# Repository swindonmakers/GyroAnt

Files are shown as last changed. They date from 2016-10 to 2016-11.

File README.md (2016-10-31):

# GyroAnt
Antweight tribute to [Gyrobot](http://www.gyrobot.co.uk/the-gyrobot.html) developed using OpenSCAD and the [OpenSCAD for Machine Design framework](https://github.com/swindonmakers/snhack.github.io/wiki/OpenSCADMD_Tutorial1).

See the [assembly, printing and sourcing guides](https://rawgit.com/swindonmakers/GyroAnt/master/hardware/docs/index.htm) for build instructions and links to the printable STLs.

https://rawgit.com/swindonmakers/GyroAnt/master/hardware/docs/index.htm

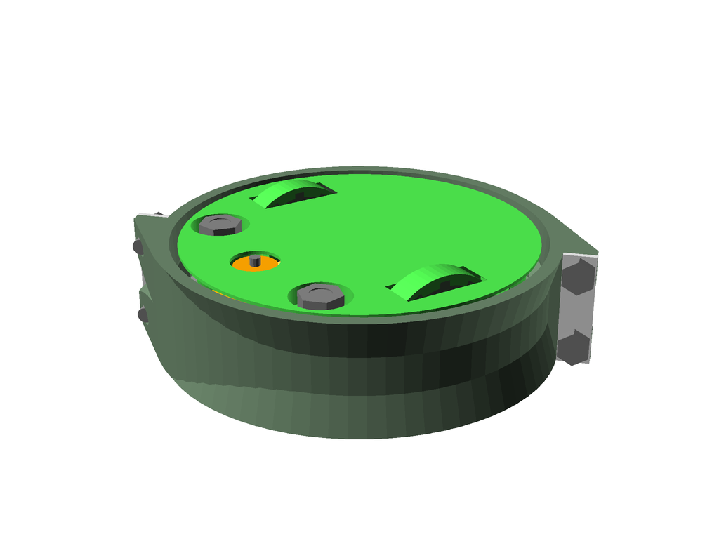
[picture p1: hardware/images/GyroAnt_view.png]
https://rawgit.com/swindonmakers/GyroAnt/master/hardware/docs/index.htm


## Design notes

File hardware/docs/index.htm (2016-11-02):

# GyroAnt Documentation

Design variants are listed below, with associated links to their assembly and printing guides. The Vitamin catalogue for the framework can be found at the bottom of the page.

## GyroAnt



### Guides

- GyroAnt Assembly Guide
- GyroAnt Printing Guide
- GyroAnt Sourcing Guide

## Vitamin Catalogue

Catalogue of the vitamins available within the Machine Design framework:

Vitamin Catalogue

NB: The catalogue may contain more vitamins than are actually used by the project

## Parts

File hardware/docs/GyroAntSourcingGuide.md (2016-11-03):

# GyroAnt
# Sourcing Guide

### 1x C2020 Micro Brushless Outrunner 3500kv 11g

Unit Cost | Source | Notes 
--- | --- | --- 
8.20 | [link](http://hobbyking.com) | 

 

### 1x DYS BLHeli 16A ESC

Unit Cost | Source | Notes 
--- | --- | --- 
3.20 | [link](http://hobbyking.com) | 

 

### 1x DasMikro Ultra Mini 8CH PPM Receiver

Unit Cost | Source | Notes 
--- | --- | --- 
9.14 | [link](http://www.banggood.com/FLYSKY-Ultra-Miniature-PPM-Signal-Output-8CH-Receiver-For-Multicopter-p-988175.html) | 

 

### 2x N20DCGearMotor

Unit Cost | Source | Notes 
--- | --- | --- 
2.64 | [link](http://cgi.ebay.co.uk/ws/eBayISAPI.dll?ViewItem&item=181946954392&var=481770476175) | 6V 200RPM version

 

### 2x O-Ring 2x10

Unit Cost | Source | Notes 
--- | --- | --- 
0 |  | No sources found

 

### 2x Stainless steel Flat Bar 6x1mm x 21mm

Unit Cost | Source | Notes 
--- | --- | --- 
0 |  | No sources found

 

### 2x Stainless steel Round Bar 2mm x 14mm

Unit Cost | Source | Notes 
--- | --- | --- 
0 |  | No sources found

 

### 2x TowerPro SG90 Driver

Unit Cost | Source | Notes 
--- | --- | --- 
2.00 | www.ebay.co.uk | 

 

### 1x Turnigy Nano-Tech 120mAh 2S 25C Lipo Pack E-Flite Compatible

Unit Cost | Source | Notes 
--- | --- | --- 
5.99 | [link](http://cgi.ebay.co.uk/ws/eBayISAPI.dll?ViewItem&item=331965220542) | 

 

### 3x 624VV 4x13x6mm V Groove Sealed Ball Bearing

Unit Cost | Source | Notes 
--- | --- | --- 
0.19 | [link](http://cgi.ebay.co.uk/ws/eBayISAPI.dll?ViewItem&item=221317556825&var=520193870489) | 

 

### 5x M4 Nut

Unit Cost | Source | Notes 
--- | --- | --- 
0.05 |  | No sources found

 

### 4x M3 hex screw x 8mm

Unit Cost | Source | Notes 
--- | --- | --- 
0.10 |  | No sources found

 

### 1x M4 hex screw x 15mm

Unit Cost | Source | Notes 
--- | --- | --- 
0.10 |  | No sources found

 

### 2x M4 hex screw x 19mm

Unit Cost | Source | Notes 
--- | --- | --- 
0.10 |  | No sources found

 

## Summary

### Total Costs

Metric | Value 
--- | --- 
Total Vitamins | 29
Total Cost (cheapest) | 37.33 GBP

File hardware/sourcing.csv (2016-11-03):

Vitamin | Cost | Source | Notes
C2020 Micro Brushless Outrunner 3500kv 11g | 8.20 | http://hobbyking.com
DYS BLHeli 16A ESC | 3.20 | http://hobbyking.com
DasMikro Ultra Mini 8CH PPM Receiver | 9.14 | http://www.banggood.com/FLYSKY-Ultra-Miniature-PPM-Signal-Output-8CH-Receiver-For-Multicopter-p-988175.html
N20DCGearMotor | 2.64 | http://cgi.ebay.co.uk/ws/eBayISAPI.dll?ViewItem&item=181946954392&var=481770476175 | 6V 200RPM version
O-Ring 2x10 | 0 |  | No sources found
Stainless steel Flat Bar 6x1mm x 21mm | 0 |  | No sources found
Stainless steel Round Bar 2mm x 14mm | 0 |  | No sources found
TowerPro SG90 Driver | 2.00 | www.ebay.co.uk
Turnigy Nano-Tech 120mAh 2S 25C Lipo Pack E-Flite Compatible | 5.99 | http://cgi.ebay.co.uk/ws/eBayISAPI.dll?ViewItem&item=331965220542
624VV 4x13x6mm V Groove Sealed Ball Bearing | 0.19 | http://cgi.ebay.co.uk/ws/eBayISAPI.dll?ViewItem&item=221317556825&var=520193870489
M4 Nut | 0.05 |  | No sources found
M3 hex screw x 8mm | 0.10 |  | No sources found
M4 hex screw x 15mm | 0.10 |  | No sources found
M4 hex screw x 19mm | 0.10 |  | No sources found

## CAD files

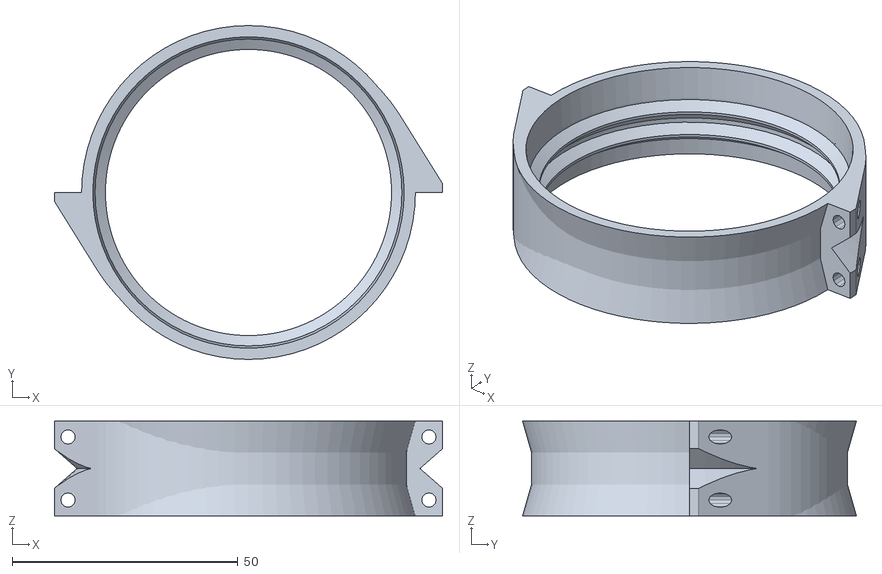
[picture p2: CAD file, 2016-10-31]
hardware/printedparts/stl/WeaponRing.stl
86.0 x 74.0 x 21.0

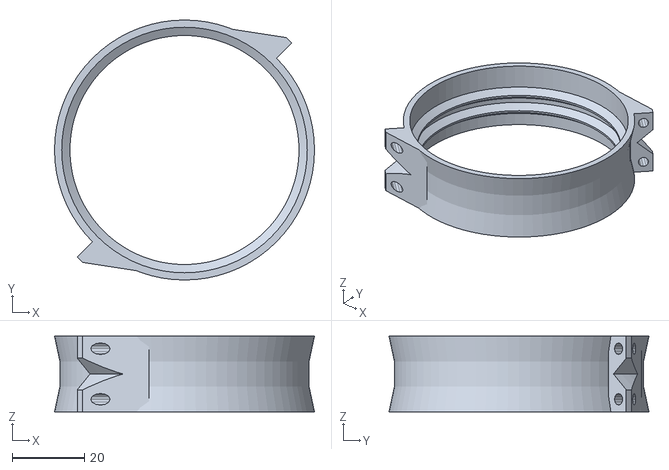
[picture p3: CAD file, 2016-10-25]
hardware/sandbox/WeaponRing.stl
72.0 x 72.0 x 21.0

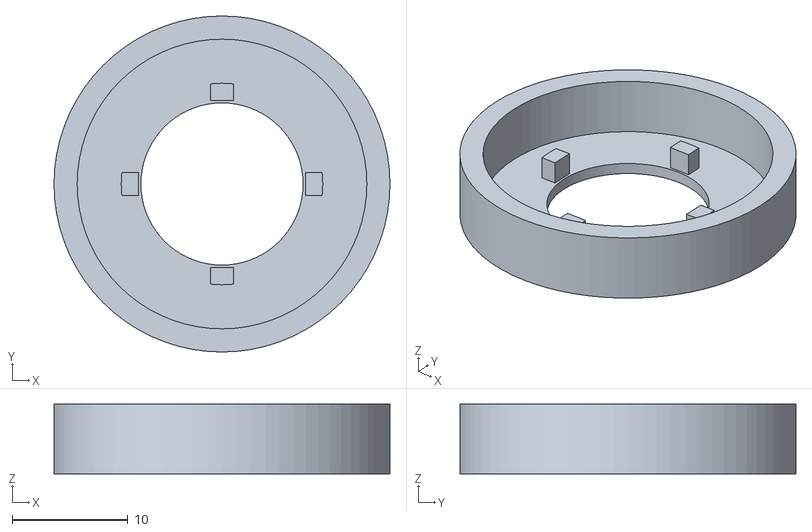
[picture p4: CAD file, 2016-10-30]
hardware/printedparts/stl/TyreMould.stl
29.0 x 29.0 x 6.00

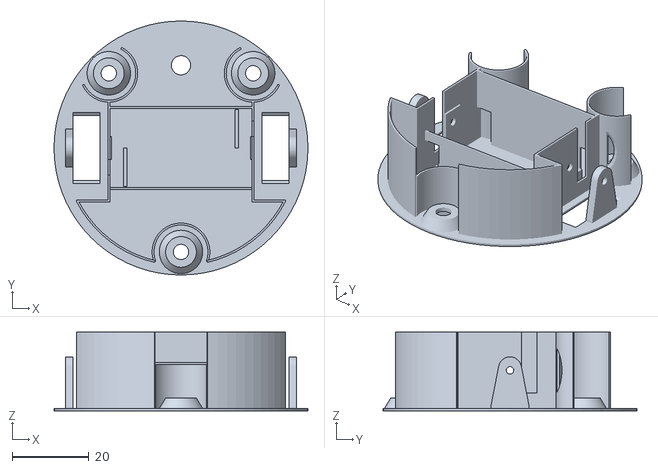
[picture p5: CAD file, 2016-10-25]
hardware/sandbox/Base.stl
66.0 x 66.0 x 20.4

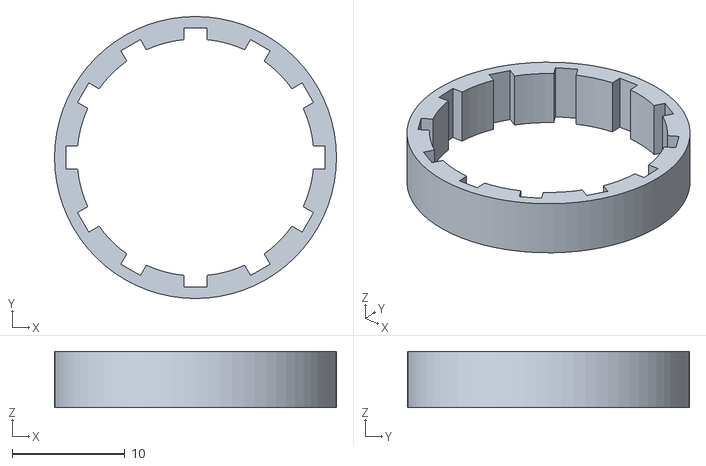
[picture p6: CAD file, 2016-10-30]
hardware/printedparts/stl/Tyre.stl
25.0 x 25.0 x 5.00

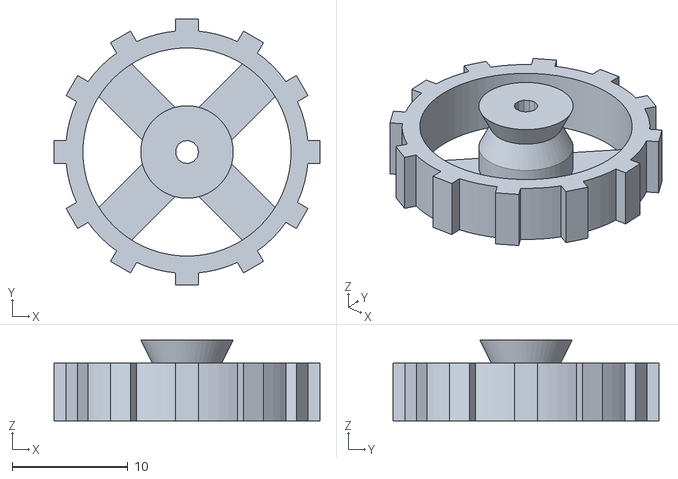
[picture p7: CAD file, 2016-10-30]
hardware/printedparts/stl/Wheel.stl
23.0 x 23.0 x 7.00

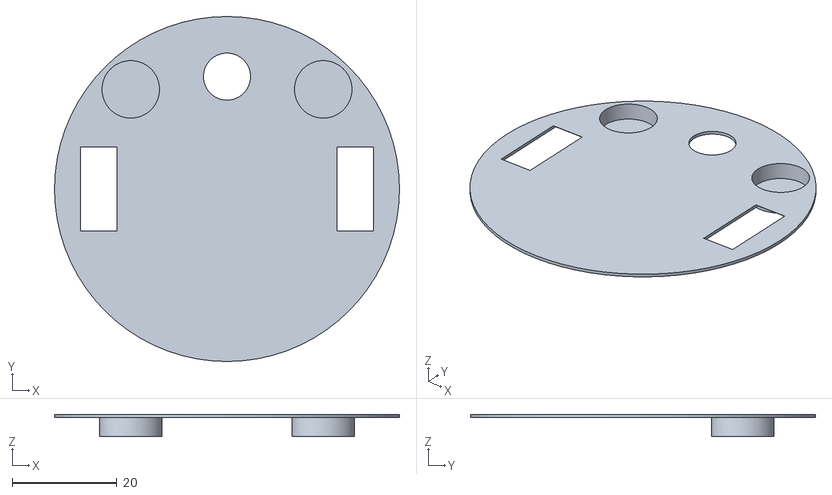
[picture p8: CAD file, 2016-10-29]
hardware/printedparts/stl/Lid.stl
66.0 x 66.0 x 4.30

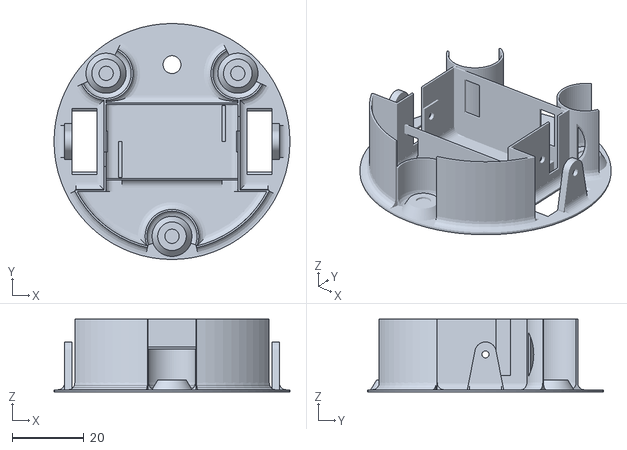
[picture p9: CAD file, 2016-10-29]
hardware/printedparts/stl/Base.stl
66.0 x 66.0 x 20.4

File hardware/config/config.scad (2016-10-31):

//
// Config
//

// Coding-style
// ------------
//
// Global variables are written in UpperCamelCase.
// A logical hierarchy should be indicated using underscores, for example:
//     StepperMotor_Connections_Axle
//
// Global short-hand references should be kept to a minimum to avoid name-collisions

// Framework configuration
include <../framework/config/config.scad>


// Put overrides to framework config here
ColourScheme = 1;


// Machine specific global parameters here
// common wall thicknesses for printed parts
DefaultWall 	= 4*perim;
ThickWall 		= 8*perim;
// short-hand
dw 				= DefaultWall;
tw 				= ThickWall;

// Global design parameters
WheelOD = 25;
TyreThickness = 2;
WeaponOR = 74/2;
RingThickness = 3;
GroundClearance = 2;
BearingAngles = [46, 134, 270];
BearingOffset = WeaponOR-RingThickness-7-0.5;
BearingHeight = 8; // from ground plane
ToothScrewSpacing = 14;



// Include all other project specific configuration files
include <utils.scad>
include <vitamins.scad>
include <cutparts.scad>
include <printedparts.scad>
include <assemblies.scad>

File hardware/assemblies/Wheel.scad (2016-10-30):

module WheelAssembly () {

    assembly("assemblies/Wheel.scad", "Wheel", str("WheelAssembly()")) {

        // generate an animation video for this assembly
        animation(title="Wheel",framesPerStep=10);

        // base part
        Wheel_STL();

        // steps
        CurStep = $ShowStep;
        step(1, "Place wheel hub into the tyre mould") {
            view(t=[0,0,0], r=[52,0,218], d=240);


            if (CurStep<3 || $ShowBOM)
                attach([[0,0,-1], [0,0,1], 0,0,0], DefConUp)
                  TyreMould_STL();
        }

        AnimT = $AnimateExplodeT;
        step(2, "Pour in rubber to overmould the tyre") {
            view(t=[0,0,0], r=[52,0,218], d=240);

            translate([0,0,0])
                scale([1,1,CurStep==2 ? AnimT : 1])
                  Tyre_STL();


        }


        step(3, "Once dry, remove the finished tyre from the mould") {
            view(t=[0,0,0], r=[52,0,218], d=240);

            if (CurStep<4 || $ShowBOM)
                attach([[0,0,-11], [0,0,-1], 0,0,0], DefConDown)
                TyreMould_STL();
        }



    }
}

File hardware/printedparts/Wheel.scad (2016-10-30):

// Connectors

Wheel_Con_Def = [[0,0,0], [0,0,-1], 0,0,0];


module Wheel_STL() {

    printedPart("printedparts/Wheel.scad", "Wheel", "Wheel_STL()") {

        view(t=[0,0,0],r=[72,0,130],d=400);

        if (DebugCoordinateFrames) frame();
        if (DebugConnectors) {
            connector(Wheel_Con_Def);
        }

        color(Level4PlasticColor) {
            if (UseSTL) {
                import(str(STLPath, "Wheel.stl"));
            } else {
                Wheel_Model();
            }
        }
    }
}


module Wheel_Model()
{
    t =1.5;
    h= 5;
    difference() {
        union() {
            // tyre
            tube(WheelOD/2 - TyreThickness, WheelOD/2-TyreThickness-t, h=h, center=false);

            // spokes
            for (i=[0:3])
                rotate([0,0,i*360/4 + 45])
                translate([0,-2,0])
                cube([WheelOD/2-TyreThickness-1, 4, 1]);

            // keys for tyre
            nk = 12;
            for (i=[0:nk-1])
                rotate([0,0,i*360/nk])
                translate([WheelOD/2-TyreThickness-1,-1,0])
                cube([TyreThickness, 2, h]);

            // hub
            cylinder(r=8/2, h=3);

            // vslot
            translate([0,0,5])
                for(i=[0,1])
                mirror([0,0,i])
                cylinder(r1=3, r2=4, h=2);
        }

        // shaft
        cylinder(r=2/2, h=100, center=true);
    }
}

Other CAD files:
hardware/GyroAnt.scad
hardware/assemblies/Final.scad
hardware/assemblies/WeaponRing.scad
hardware/config/assemblies.scad
hardware/config/cutparts.scad
hardware/config/printedparts.scad
hardware/config/utils.scad
hardware/config/vitamins.scad
hardware/cutparts/HammerPlate.scad
hardware/printedparts/Base.scad
hardware/printedparts/Lid.scad
hardware/printedparts/Tyre.scad
hardware/printedparts/TyreMould.scad
hardware/printedparts/WeaponRing.scad
hardware/sandbox/animatedAssembly.scad
hardware/sandbox/assembly_FinalAssembly.scad
hardware/sandbox/assembly_WeaponRingAssembly.scad
hardware/sandbox/assembly_WheelAssembly.scad
hardware/sandbox/cutpart_Axle.scad
hardware/sandbox/cutpart_HammerPlate.scad
hardware/sandbox/layout.scad
hardware/sandbox/printedpart_Base.scad
hardware/sandbox/printedpart_Lid.scad
hardware/sandbox/printedpart_Tyre.scad
hardware/sandbox/printedpart_TyreMould.scad
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

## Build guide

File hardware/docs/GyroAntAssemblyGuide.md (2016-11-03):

# GyroAnt
# Assembly Guide

view

## Bill of Materials

Make sure you have all of the following parts before you begin.

### Vitamins

Qty | Vitamin | Image
--- | --- | ---
1 | [C2020 Micro Brushless Outrunner 3500kv 11g]() |  | 
1 | [DYS BLHeli 16A ESC]() |  | 
1 | [DasMikro Ultra Mini 8CH PPM Receiver]() |  | 
2 | [N20DCGearMotor]() |  | 
2 | [O-Ring 2x10]() |  | 
2 | [Stainless steel Flat Bar 6x1mm x 21mm]() |  | 
2 | [Stainless steel Round Bar 2mm x 14mm]() |  | 
2 | [TowerPro SG90 Driver]() |  | 
1 | [Turnigy Nano-Tech 120mAh 2S 25C Lipo Pack E-Flite Compatible]() |  | 
3 | [624VV 4x13x6mm V Groove Sealed Ball Bearing]() |  | 
5 | [M4 Nut]() |  | 
4 | [M3 hex screw x 8mm]() |  | 
1 | [M4 hex screw x 15mm]() |  | 
2 | [M4 hex screw x 19mm]() |  | 

### Cut Parts

Qty | Part Name | Image
--- | --- | ---
2 | HammerPlate |  | 

### Printed Parts

Qty | Part Name | Image
--- | --- | ---
1 | [Base](../printedparts/stl/Base.stl) |  | 
1 | [Lid](../printedparts/stl/Lid.stl) |  | 
4 | [Tyre Mould](../printedparts/stl/TyreMould.stl) |  | 
2 | [Tyre](../printedparts/stl/Tyre.stl) |  | 
1 | [WeaponRing](../printedparts/stl/WeaponRing.stl) |  | 
2 | [Wheel](../printedparts/stl/Wheel.stl) |  | 

**Plastic Required**

32.6cm3, 0.04KG,  approx: 0.53 GBP

# Cutting Instructions

## HammerPlate (x2)

### Vitamins

Qty | Vitamin | Image
--- | --- | ---
2 | [Stainless steel Flat Bar 6x1mm x 21mm]() |  | 

### Fabrication Steps

1. Cut a small piece of 1mm steel plate to size

2. Drill two 3mm dia holes at 14mm spacing


# Assembly Instructions

## Wheel (x2)

### Printed Parts

Qty | Part Name | Image
--- | --- | ---
4 | [Tyre Mould](../printedparts/stl/TyreMould.stl) |  | 
2 | [Tyre](../printedparts/stl/Tyre.stl) |  | 
2 | [Wheel](../printedparts/stl/Wheel.stl) |  | 

### Assembly Animation

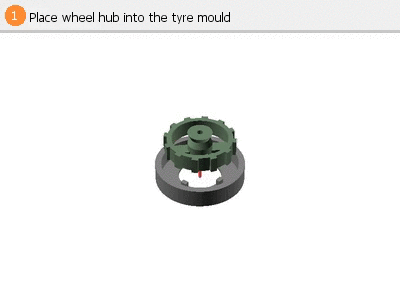
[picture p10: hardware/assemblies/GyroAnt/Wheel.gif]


### Assembly Steps

1. Place wheel hub into the tyre mould
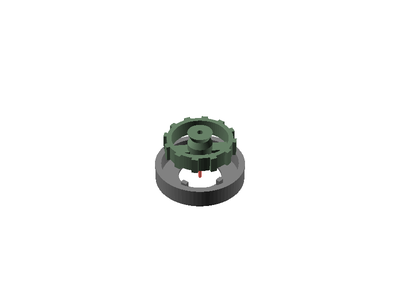
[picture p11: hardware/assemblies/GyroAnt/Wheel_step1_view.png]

2. Pour in rubber to overmould the tyre
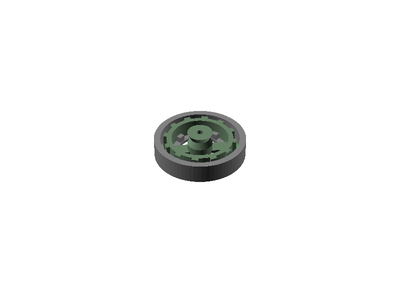
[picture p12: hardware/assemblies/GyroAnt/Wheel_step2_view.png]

3. Once dry, remove the finished tyre from the mould
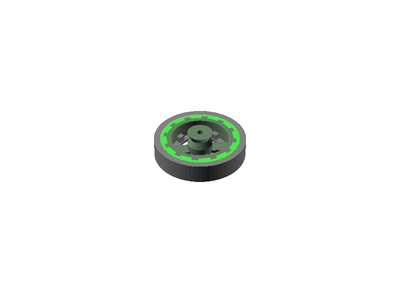
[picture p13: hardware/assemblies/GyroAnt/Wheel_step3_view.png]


## WeaponRing

### Vitamins

Qty | Vitamin | Image
--- | --- | ---
4 | [M3 hex screw x 8mm]() |  | 

### Printed Parts

Qty | Part Name | Image
--- | --- | ---
1 | [WeaponRing](../printedparts/stl/WeaponRing.stl) |  | 

### Assembly Animation

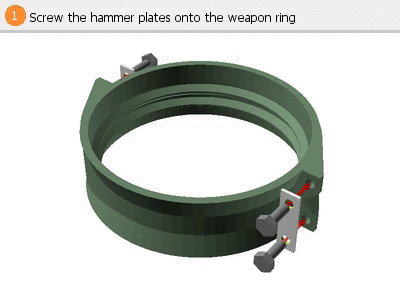
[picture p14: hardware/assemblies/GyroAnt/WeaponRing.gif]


### Assembly Steps

1. Screw the hammer plates onto the weapon ring
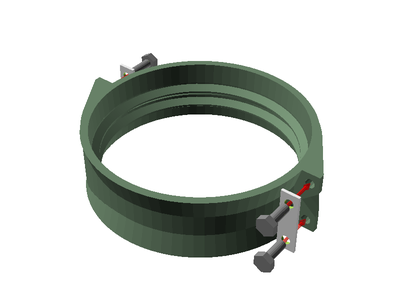
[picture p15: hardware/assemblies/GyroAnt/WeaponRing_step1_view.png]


## Final

### Vitamins

Qty | Vitamin | Image
--- | --- | ---
1 | [C2020 Micro Brushless Outrunner 3500kv 11g]() |  | 
1 | [DYS BLHeli 16A ESC]() |  | 
1 | [DasMikro Ultra Mini 8CH PPM Receiver]() |  | 
2 | [N20DCGearMotor]() |  | 
2 | [O-Ring 2x10]() |  | 
2 | [Stainless steel Round Bar 2mm x 14mm]() |  | 
2 | [TowerPro SG90 Driver]() |  | 
1 | [Turnigy Nano-Tech 120mAh 2S 25C Lipo Pack E-Flite Compatible]() |  | 
3 | [624VV 4x13x6mm V Groove Sealed Ball Bearing]() |  | 
5 | [M4 Nut]() |  | 
1 | [M4 hex screw x 15mm]() |  | 
2 | [M4 hex screw x 19mm]() |  | 

### Printed Parts

Qty | Part Name | Image
--- | --- | ---
1 | [Base](../printedparts/stl/Base.stl) |  | 
1 | [Lid](../printedparts/stl/Lid.stl) |  | 

### Sub-Assemblies

Qty | Name 
--- | --- 
2 | Wheel
1 | WeaponRing

### Assembly Animation



### Assembly Steps

1. Locate wheels and insert axles
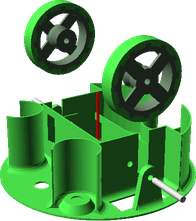
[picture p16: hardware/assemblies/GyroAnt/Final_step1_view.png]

2. Fit motors and o-rings
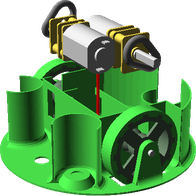
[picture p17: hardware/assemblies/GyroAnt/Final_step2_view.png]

3. Fit weapon outrunner
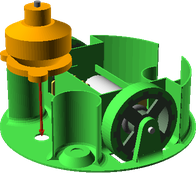
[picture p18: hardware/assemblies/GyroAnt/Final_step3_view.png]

4. Slide weapon ring over base, along with v bearings
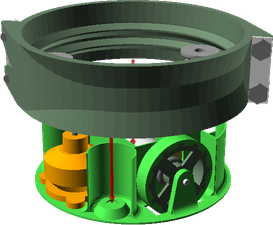
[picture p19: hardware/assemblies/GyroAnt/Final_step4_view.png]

5. Secure bearings for weapon ring
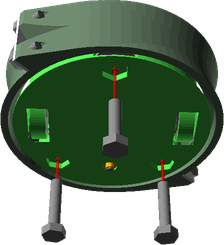
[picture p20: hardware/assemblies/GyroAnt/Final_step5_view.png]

6. Wire up Rx, ESCs and motors
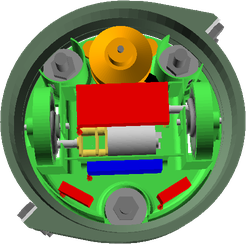
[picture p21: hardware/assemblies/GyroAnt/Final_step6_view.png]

7. Install battery
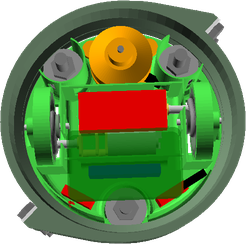
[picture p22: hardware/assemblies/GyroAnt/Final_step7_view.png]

8. Fit lid
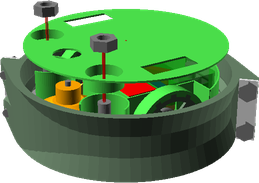
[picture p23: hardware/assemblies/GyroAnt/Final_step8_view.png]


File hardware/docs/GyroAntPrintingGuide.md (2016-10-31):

# GyroAnt
# Printing Guide

### Base

Metric | Value 
--- | --- 
Quantity | 1
STL | [Base](../printedparts/stl/Base.stl)
Plastic (Kg) | 0.01
Plastic (cm3) | 6.3
Approx Plastic Cost | 0.12 GBP



### Lid

Metric | Value 
--- | --- 
Quantity | 1
STL | [Lid](../printedparts/stl/Lid.stl)
Plastic (Kg) | 0.0
Plastic (cm3) | 2.3
Approx Plastic Cost | 0.04 GBP



### Tyre Mould

Metric | Value 
--- | --- 
Quantity | 4
STL | [Tyre Mould](../printedparts/stl/TyreMould.stl)
Plastic (Kg) | 0.01
Plastic (cm3) | 6.0
Approx Plastic Cost | 0.11 GBP



### Tyre

Metric | Value 
--- | --- 
Quantity | 2
STL | [Tyre](../printedparts/stl/Tyre.stl)
Plastic (Kg) | 0.0
Plastic (cm3) | 1.2
Approx Plastic Cost | 0.02 GBP



### WeaponRing

Metric | Value 
--- | --- 
Quantity | 1
STL | [WeaponRing](../printedparts/stl/WeaponRing.stl)
Plastic (Kg) | 0.02
Plastic (cm3) | 14.4
Approx Plastic Cost | 0.27 GBP



### Wheel

Metric | Value 
--- | --- 
Quantity | 2
STL | [Wheel](../printedparts/stl/Wheel.stl)
Plastic (Kg) | 0.0
Plastic (cm3) | 2.4
Approx Plastic Cost | 0.04 GBP



## Summary

### Statistics

Metric | Value 
--- | --- 
Total Parts | 11
Total Plastic (Kg) | 0.04KG
Total Plastic (cm3) | 32.6cm3
Approx Plastic Cost | 0.61 GBP

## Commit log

2016-10-25 Transfer from dropbox
    [3DRRadio.scad, APM25.scad, AluProParts.scad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]
2016-10-25 Refactored into proper assemblies, parts and vitamins
    [Base.scad, Base.stl, C2020BrushlessOutrunner.scad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]
2016-10-25 Corrected steps, rebuilt
    [Final.scad]
2016-10-25 Automated animated assembly videos
    [Final.scad, animatedAssembly.scad, maths.scad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]
2016-10-25 Added automatic view transitions and final turntable
    [Final.scad, assemblies.scad, temp.scad]
2016-10-25 Fixed small bugs, added titles
    [Final.scad, assemblies.scad]
2016-10-27 Added o-rings, refined animation process
    [Final.scad, N20DCGearMotor.scad, ORing.scad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]
2016-10-27 Axle defined as cut part, using stock metal
    [Axle.scad, Final.scad, Material.scad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]
2016-10-27 auto build
    [Base.scad, Base.stl, Lid.scad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]
2016-10-27 Added fillets to base
    [Base.scad, Base.stl, moreShapes.scad]
2016-10-27 Updated main view
    [GyroAnt.scad, IgusDrylinNRailNS0127100mm.stl, MicroServo_Body.stl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]
2016-10-27 Remove old assign() calls
    [ribbonCable.scad, screw.scad]
2016-10-27 Fix animate bug with STLs, Simplify axle to just StockMetal
    [Axle.scad, Final.scad, assembly_FinalAssembly.scad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]
2016-10-27 Moved weaponRing into an assembly
    [Final.scad, HammerPlate.scad, StockMetal.scad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]
2016-10-27 Minor bug in using STL when rendering views
2016-10-28 Started populating sources
    [sourcing.csv]
2016-10-28 Improved build arguments, added animations to build process
    [WeaponRing.scad, assemblies.scad, temp.scad]
2016-10-28 Simplified catalogue build
    removed unnecessary compilation to STL
2016-10-28 Integrated animations into guide generation
    [Final.scad, WeaponRing.scad, temp.scad]
2016-10-30 Updated weaponring
    [WeaponRing.scad, WeaponRing.stl]
2016-10-30 Updated WeaponRing again
    Tweaking upper v ring for improved printability
    [WeaponRing.scad, WeaponRing.stl]
2016-10-30 Fixing mistake on weaponring
    left the debug notch in :(
    [WeaponRing.scad, WeaponRing.stl]
2016-10-30 Over moulded tyre
    [Final.scad, Tyre.scad, Tyre.stl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]
2016-10-30 Added TyreMould to build
    [TyreMould.stl, Wheel.scad]
2016-10-30 moving framework into subdir
    in prep for submodule
    [3DRRadio.scad, APM25.scad, AluProParts.scad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]
2016-10-31 Further refinements and path corrections
    [Base.stl, DF13Connector.scad, Demo_Renderer.scad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]
2016-10-31 Further layout refinements, path updates
    [assemblies.scad, assembly.scad, cutpart.scad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]
2016-10-31 Update catalogue paths
    [temp.scad]
2016-10-31 Fixing vitamin sourcing
    [sourcing.csv]
2016-10-31 Enhanced sourcing to populate missing vitamins
    [sourcing.csv]
2016-10-31 Stripping out framework codebase
    … to be replaced with submodule
    [3DRRadio.scad, APM25.scad, AluProParts.scad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]
2016-10-31 Embed framework submodule
2016-10-31 Rebuild after framework fixes
    [Base.stl, Lid.stl, Tyre.stl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]
2016-11-02 Updated framework
2016-11-03 Added default view to hammer plate and rebuild
    [HammerPlate.scad]
2016-11-03 Updated sourcing
    [sourcing.csv]
